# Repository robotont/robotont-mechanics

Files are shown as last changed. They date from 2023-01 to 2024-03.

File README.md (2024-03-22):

# robotont-mechanics

This repository contains models of mechanical parts of Robotont.
The latest release of Robotont is gen3.0.
Gen 3 is developed in SolidWorks (Student version), but a STEP assembly is also provided for modeling, as well as 3MF files for 3D-printing.

## Chassis overview

The main chassis is divided into 5 modules:

+ Frame module
+ Motor module
+ Camera module
+ Computer module
+ Battery module

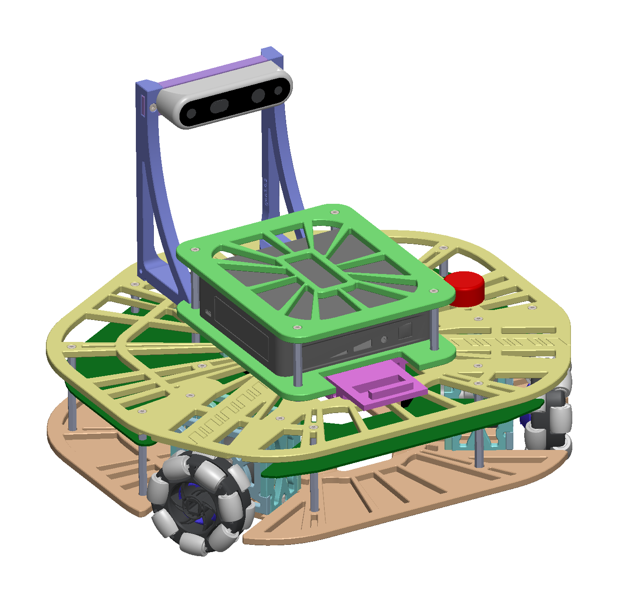
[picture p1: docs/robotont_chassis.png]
Robotont gen3.0 chassis with Intel RealSense and Intel Nuc


## Production

To reproduce Robotont, production files are provided in [production](main-chassis/production/) folder.
The 3MF files contain the print settings optimised for Prusa MK3S, as well as the grouping of parts for printing.

To develop and change Robotont, SolidWorks model files are provided, along with STEP for use with other modeling software.

## Getting started

Print the calibration parts in the [calibration.3mf print project](main-chassis/production/3mf/).
If the two halves fit together and come apart easily, there are no issues with elephant foot and all surfaces are printed cleanly, proceed with printing out all the other print projects in the [3mf folder](main-chassis/production/3mf/).
If there are issues, tune the 3D-printer settings until the calibration piece is printed well, then apply the settings to all of the print projects.

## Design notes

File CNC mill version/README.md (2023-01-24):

# robotont-mechanics
Robotont ver 3.0 is the latest release of the Robotont.

This repository is maintained by Renno Raudmäe renno.raudmae@ut.ee
If you want to make modifications on Robotont and you think that it would be cool if it is available 
for the others as well, then let me know.

Main development is so far done in SolidEdge ST10 - academic version.

Production files are also available in STEP either in STL.

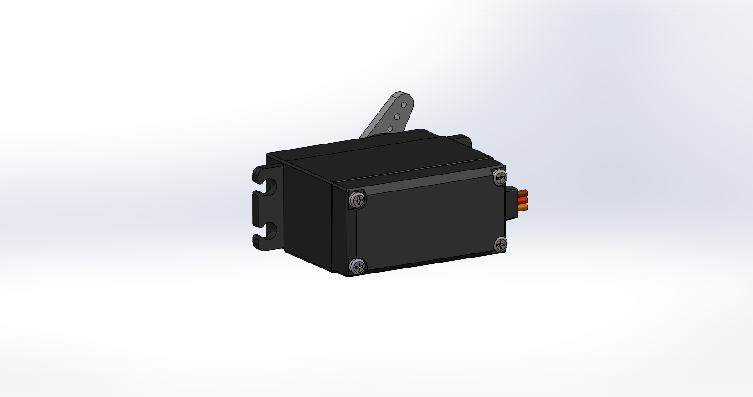
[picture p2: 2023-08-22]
main-chassis/frame_module/extension_servo_slot/towerpro_mg996r_servo/MG996R SBORKA03.PNG

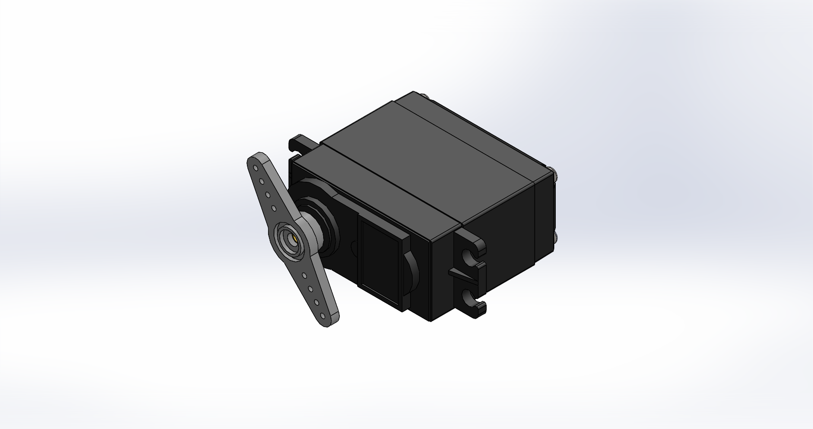
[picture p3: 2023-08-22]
main-chassis/frame_module/extension_servo_slot/towerpro_mg996r_servo/MG996R SBORKA02.PNG

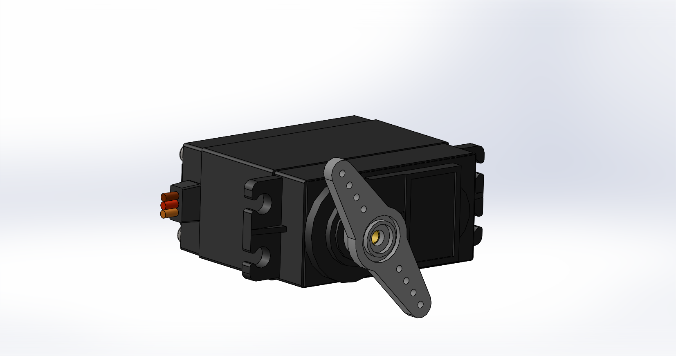
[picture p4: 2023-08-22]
main-chassis/frame_module/extension_servo_slot/towerpro_mg996r_servo/MG996R SBORKA.PNG

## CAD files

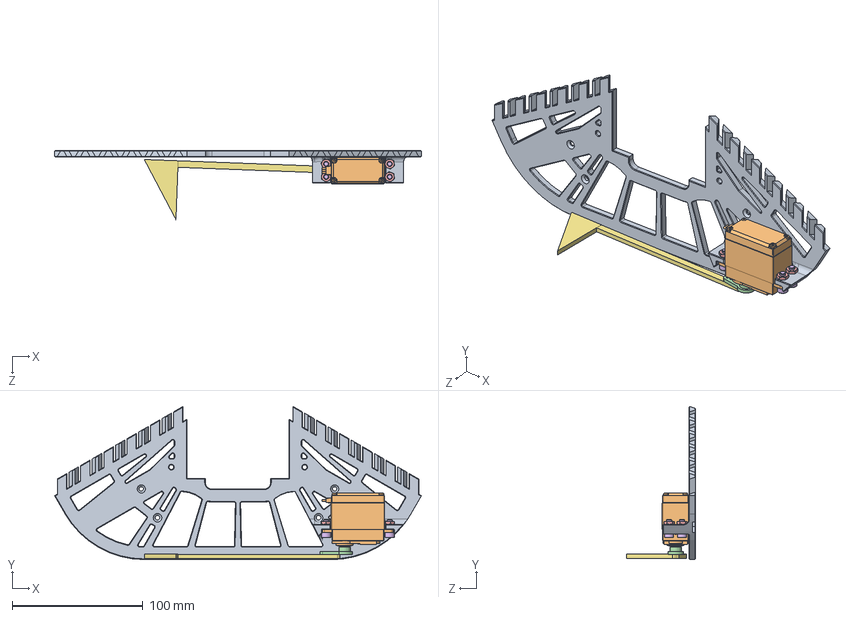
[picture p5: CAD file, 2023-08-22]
main-chassis/frame_module/extension_servo_slot/frame_top_front_servoslot.SLDASM
280.8 x 117.2 x 52.9 mm
top_plate_front_v2-0
Servo MG996R
Servo MG996R Shaft
Servo MG996R arm01
hex thin nut chamfered gradeab_iso x 4
socket head cap screw_iso x 4
demo_flag

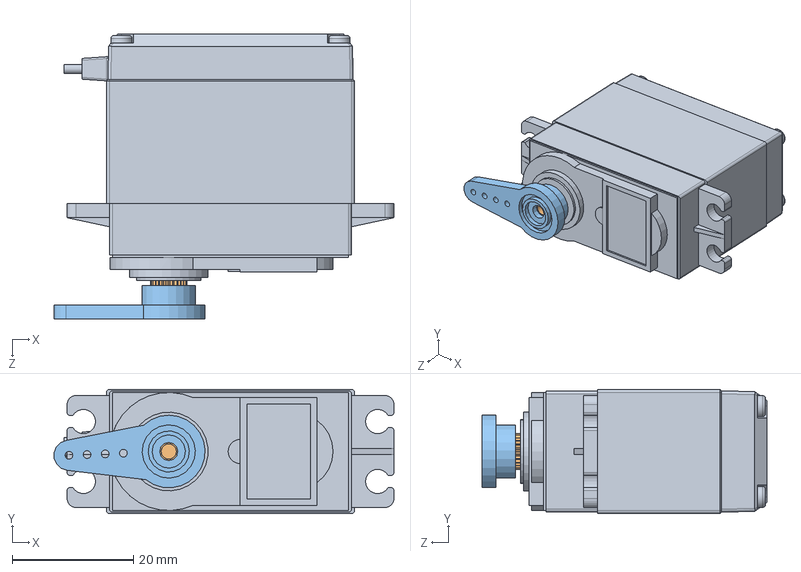
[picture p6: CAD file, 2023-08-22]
main-chassis/frame_module/extension_servo_slot/towerpro_mg996r_servo/MG996R SERVO/MG996R SBORKA.SLDASM
56.2 x 20.5 x 47.0 mm
Servo MG996R
Servo MG996R Shaft
Servo MG996R arm01

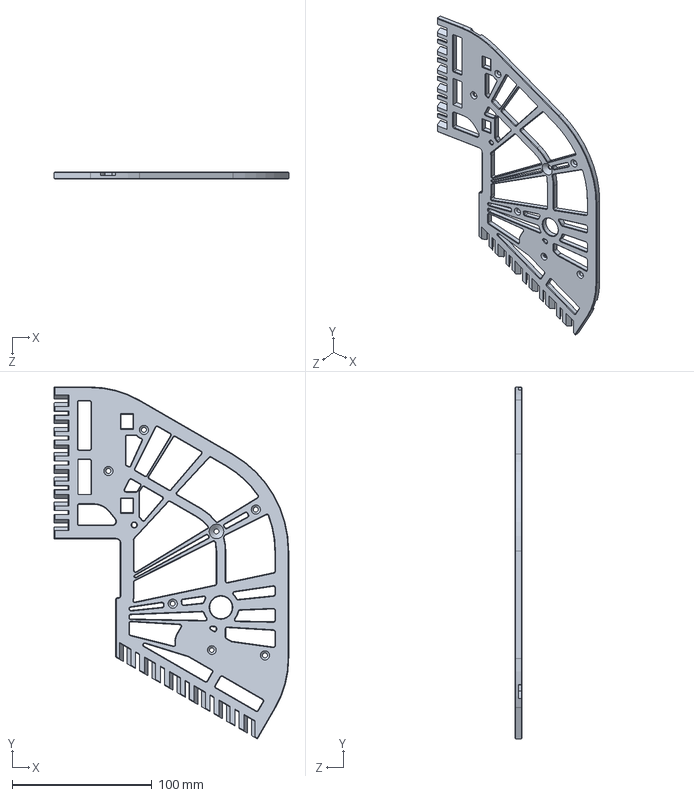
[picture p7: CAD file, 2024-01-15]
main-chassis/frame_module/frame_top.SLDASM
167.8 x 251.8 x 5.00 mm

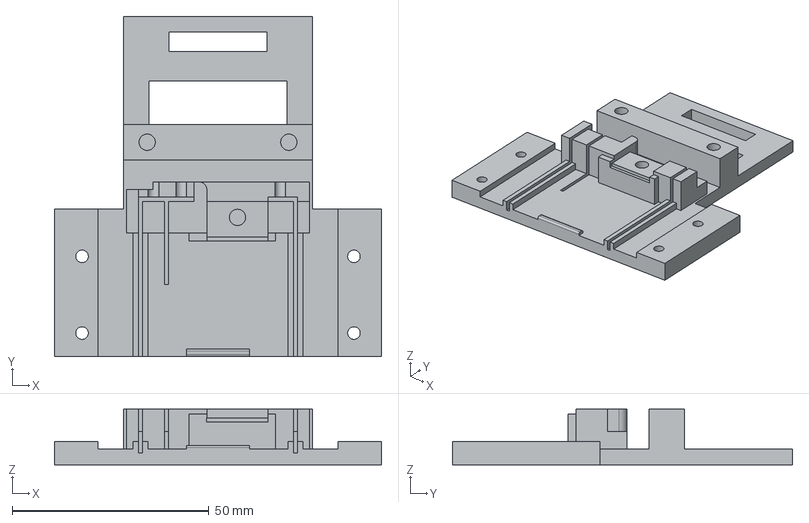
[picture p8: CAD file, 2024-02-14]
main-chassis/battery_module/step/battery_main.stp
83.1 x 86.5 x 14.2 mm

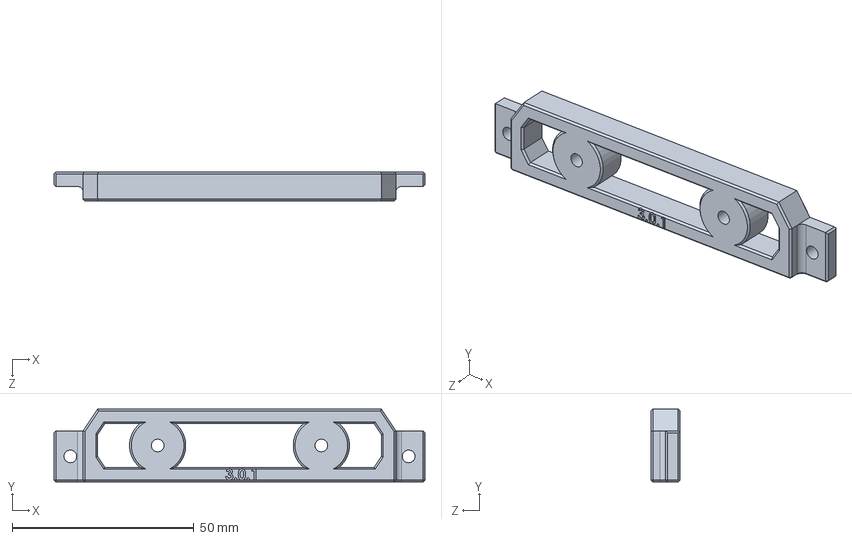
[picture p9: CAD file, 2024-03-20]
main-chassis/camera_module/camera_back.SLDPRT
102.0 x 20.0 x 8.00 mm

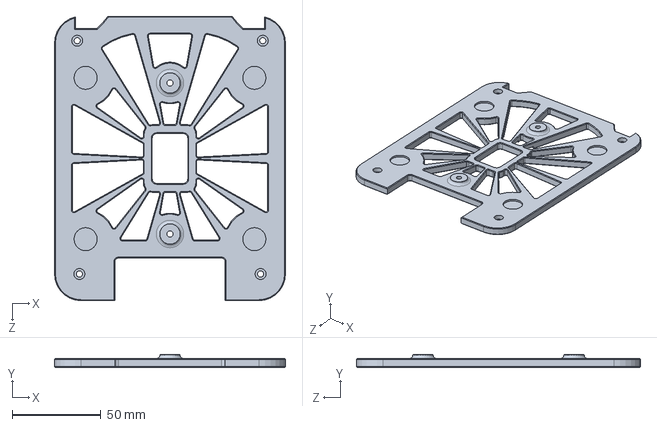
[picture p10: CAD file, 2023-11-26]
main-chassis/computer_module/computer_bottom.SLDPRT
130.0 x 7.20 x 160.0 mm

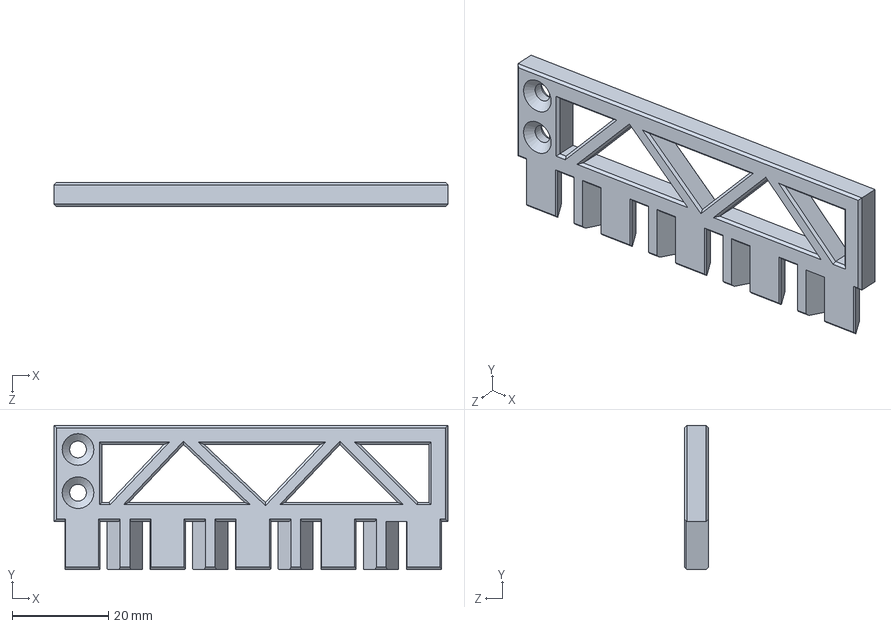
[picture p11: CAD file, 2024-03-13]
main-chassis/extras/calibration_1.SLDPRT
82.0 x 30.0 x 5.00 mm

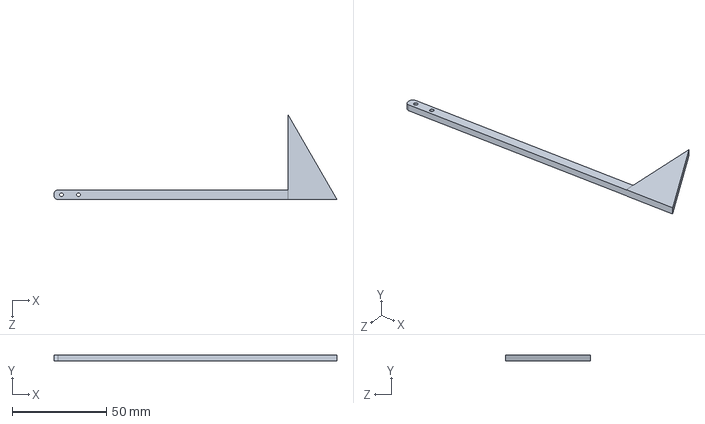
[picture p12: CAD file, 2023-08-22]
main-chassis/frame_module/extension_servo_slot/demo_flag.SLDPRT
150.0 x 3.20 x 45.0 mm

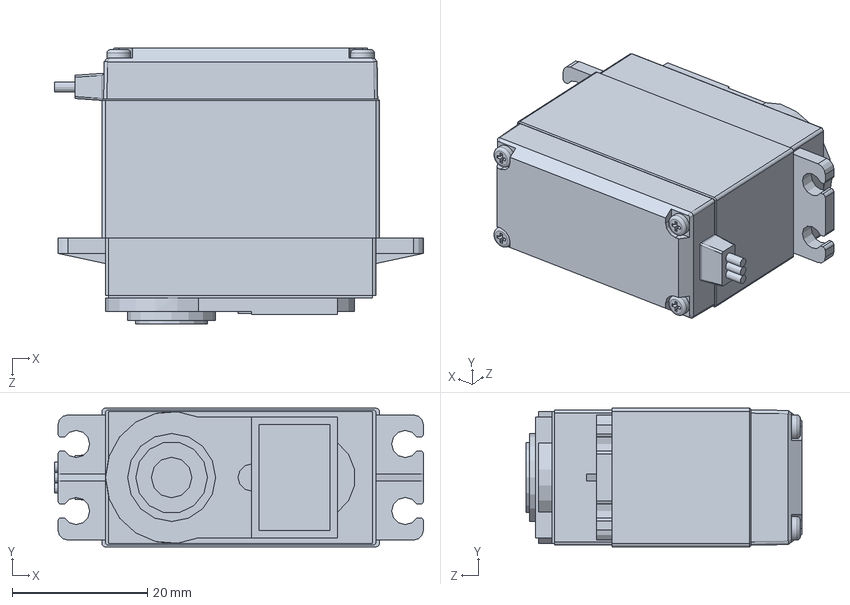
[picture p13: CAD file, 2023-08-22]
main-chassis/frame_module/extension_servo_slot/towerpro_mg996r_servo/MG996R SERVO/Servo MG996R.SLDPRT
54.5 x 20.5 x 40.7 mm

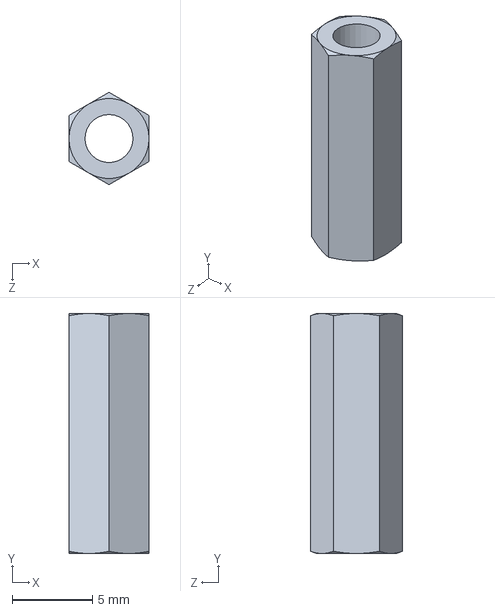
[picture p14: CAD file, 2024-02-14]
main-chassis/frame_module/fastenings/spacer_15mm.SLDPRT
5.00 x 15.0 x 5.77 mm

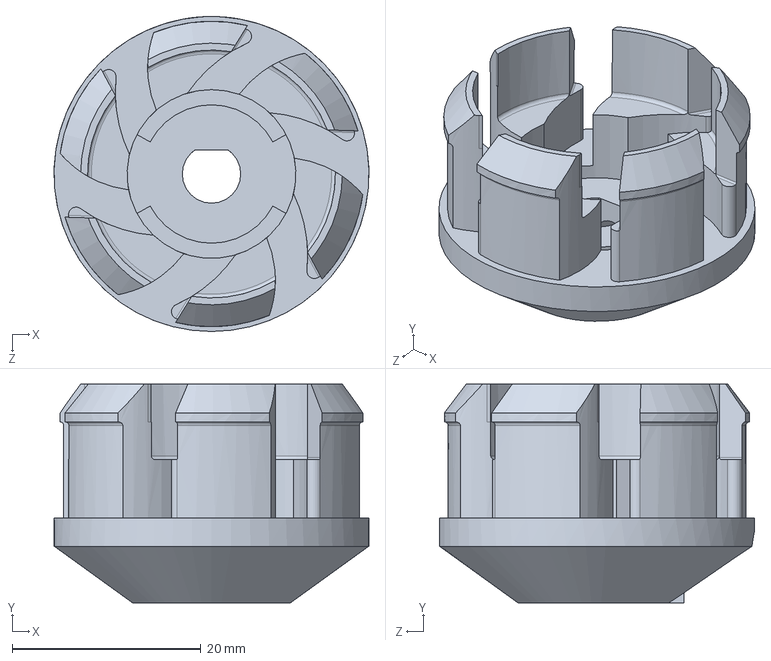
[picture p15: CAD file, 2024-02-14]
main-chassis/motor_module/motor_coupler.SLDPRT
33.4 x 23.2 x 33.4 mm

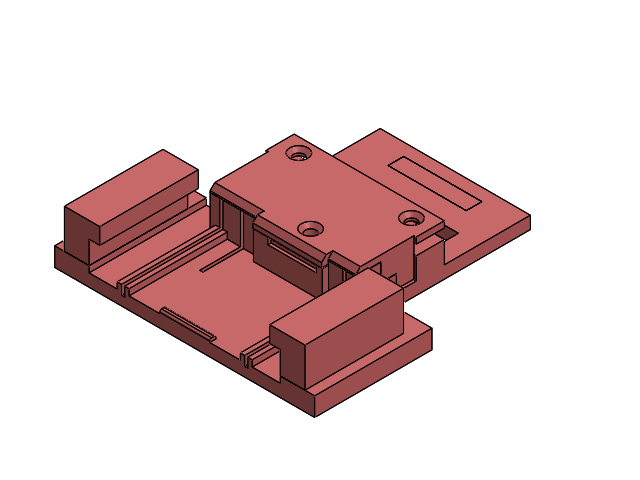
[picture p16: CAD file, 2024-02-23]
main-chassis/battery_module/battery_module.SLDASM
battery_side x 2
battery_main
battery_cap
battery_handle

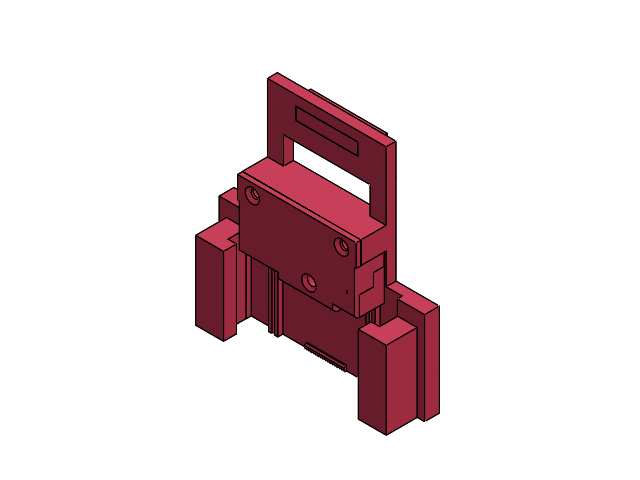
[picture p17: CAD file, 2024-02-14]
main-chassis/battery_module/step/battery_slider.SLDASM
battery_locking_slider
locking_slider_1211_side.stp x 2
handle.stp
Locking_cap.stp

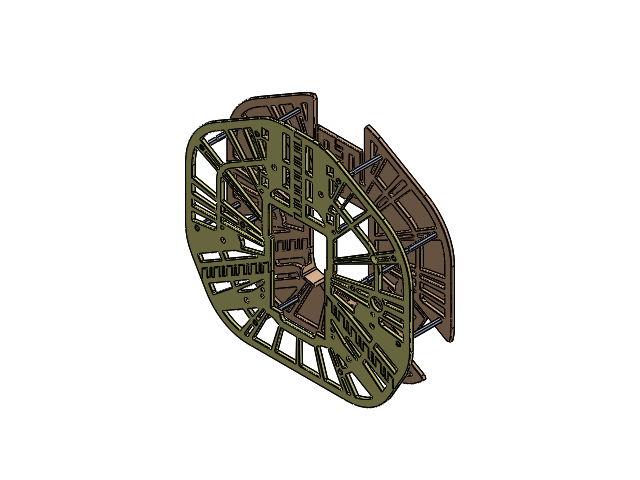
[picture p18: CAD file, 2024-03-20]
main-chassis/frame_module/frame_module.SLDASM
frame_bottom_left
frame_bottom_right
frame_bottom_front
frame_top_left
frame_top_right
frame_top_front
spacer_40mm x 12
spacer_15mm x 12
hexa csunk flathd screw_iso x 22

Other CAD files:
main-chassis/extras/calibration.SLDASM
main-chassis/camera_module/camera_module.SLDASM
main-chassis/frame_module/frame_bottom.SLDASM
main-chassis/production/stl/battery_main.STL
main-chassis/battery_module/battery_cap.SLDPRT
main-chassis/battery_module/battery_handle.SLDPRT
main-chassis/battery_module/battery_main.SLDPRT
main-chassis/battery_module/battery_side.SLDPRT
main-chassis/battery_module/step/battery_cap.stp
main-chassis/battery_module/step/battery_handle.stp
main-chassis/battery_module/step/battery_side.stp
main-chassis/camera_module/Realsense_D435.stp
main-chassis/camera_module/camera_left.SLDPRT
main-chassis/camera_module/camera_right.SLDPRT
main-chassis/computer_module/computer_top.SLDPRT
main-chassis/extras/calibration_2.SLDPRT
main-chassis/extras/encoder_button.SLDPRT
main-chassis/extras/power_button.SLDPRT
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

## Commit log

2022-06-17 Files added into folder
    Files added into folder
    [battery_cap.stp, battery_trigger.stp, bottom_plate.stp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]
2022-12-20 ver 3.0 commit
    ver 3.0 commit
    [276-1902-010 Rev1.cfg, 2_75_Omni-Directional_Wheel.cfg, 3D_print_Tip.stl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]
2023-01-24 assembly fixes January
    assembly fixes January
    [Battery_Trigger_v2.1.1 v2.step, Battery_Trigger_v2.1.1 v2.stp, Battery_cap_v2.1 v1.step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]
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2023-02-16 removed JST connector and shortened pcb length
2023-02-16 modified locking mechanism assembly
    [locking_mechanism.cfg]
2023-02-22 deleted Wheel Module folder
    [276-1902-010 Rev1.cfg, 2_75_Omni-Directional_Wheel.cfg, Linear_tapp_module.cfg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]
2023-02-22 Added Wheel module folder where motor position is adjusted to raise robot clearance from ground
    [276-1902-010 Rev1.cfg, Linear_tapp_module.cfg, omni_wheel_2.75inch.cfg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]
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2023-02-22 changed top plate and bottom plate distance back to original 55mm
    [Robot_assembly_v2.1_grouped.cfg]
2023-02-23 removed double copy part which was duplicated by accident
    [Robot_assembly_v2.1_grouped.cfg]
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2023-06-21 wheel bushing
    3d printabel bushing added
    [moyeux_print.STL, moyeux_print_2.STL, moyeux_print_m3.STL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]
2023-08-22 3D-printable chassis for gen 3.0.
    [BDSG-37-40-R150_motor.stp, MG996R SBORKA.SLDASM, PCB_shape.SLDPRT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]
2023-09-28 Moved camera position 20 mm lower to better fit the robot into the kit.
    [camera_left.SLDPRT, camera_right.SLDPRT]
2023-09-28 Updated frame_bottom_front:
    * Updated model by added supports for keeping the Makita battery from hitting the PCB.
    * Updated assemblies.
    [frame_bottom.SLDASM, frame_bottom_front.SLDPRT, frame_module.SLDASM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]
2023-11-16 Minor: changed colour of camera back plate
    [PCB_shape.SLDPRT, camera_back.SLDPRT, camera_module.SLDASM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]
2023-11-26 Spacer FF -> MF
    [spacer_6mm.SLDPRT]
2023-11-26 Frame module top right gen3.0.2 duplicate file fix
    [frame_top.SLDASM, frame_top_right.SLDPRT, frame_top_right_gen3-0-2.SLDPRT]
2023-11-26 Deleted old redundant version gen3.0.1 of frame module top left.
    [top_plate_back_left.SLDPRT]
2023-11-26 Replaced M3x10 bolts with M3x8 bolts, changed camera module back accordingly.
    [camera_back.SLDPRT, camera_module.SLDASM]
2023-11-26 Added chamfers to camera module back 90-degree inner corners (gen3.0.1).
    [camera_back.SLDPRT, camera_module.SLDASM]
2023-11-26 Replaced Mx10 bolts with M3x8 bolts, mde changes in computer module bottom accordingly. Increased NUC feet holes (d=11.2 -> d=13) to allow NUC gen10 to also fit.
    [computer_bottom.SLDPRT, computer_top.SLDPRT]
2024-01-09 Added new versions to camera module + computer module print projects.
    [cam_comp_1.3mf, cam_comp_2.3mf]
2024-01-09 Added STL files of new versions.
    [camera_back_gen3-0-1.STL, camera_left_gen3-0-2.STL, camera_right_gen3-0-2.STL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]
2024-01-09 Added power button and encoder button models and production files.
    [encoder_and_power_button.3mf, encoder_button.SLDPRT, encoder_button_v4.STL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]
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2024-01-15 Made bolt hole deeper in motor module side.
    [motor_side.SLDPRT]
2024-01-15 Replaced with latest version (gen3.0.3).
    [frame_bottom_front.3mf]
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2024-01-15 Updated motor module pieces production files with latest version of motor module side (gen3-0-3).
    [motor_all.3mf, motor_side_gen3-0-3.STL]
2024-01-15 Added new version of frame bottom front (gen3.0.3) STL file.
    [frame_bottom_front_gen3-0-3.STL]
2024-01-15 Added power button and encoder button.
    [cam_comp_2.3mf]
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2024-01-15 Renamed badly named files.
    [computer_top_gen3-0-0.STL, frame_bottom_left_gen3-0-1.STL, frame_bottom_right_gen3-0-1.STL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]
2024-01-15 Deleted old legacy STL files.
    [bottom_plate_front_gen3-0-1.STL, camera_back_plate_gen3-0-0.STL, camera_side_support_left_gen3-0-1.STL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]
2024-02-14 Minor fixes
    [camera_back.SLDPRT, camera_left.SLDPRT, camera_module.SLDASM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]
2024-02-14 Deleted files with no relevance in gen 3, as they are only related to gen 2.
    [276-1902-010 Rev1.cfg, 3D_print_Tip.stl, 3D_print_Tip.stp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]
2024-02-14 Added motor and omniwheel STEP files.
    [276-1902-003 Rev1.stp.SLDPRT, 276-1902-011 Rev1.stp.SLDPRT, 276-1902-012 Rev1.stp.SLDPRT]
2024-02-14 Added printing files that include the buttons and motor couplers
    [cam_comp_alternative_1.3mf, cam_comp_alternative_2.3mf, motor_all_alternative.3mf]
2024-02-14 Folder refacto: moved folder
    [276-1902-003 Rev1.stp.SLDPRT, 276-1902-011 Rev1.stp.SLDPRT, 276-1902-012 Rev1.stp.SLDPRT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]
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2024-02-14 Nothing changed, just rebuild of assembly.
    [camera_module.SLDASM, frame_module.SLDASM]
2024-02-14 Folder refacto: moved files
    [encoder_button.SLDPRT, encoder_button_v4.STL, power_button.SLDPRT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]
2024-02-14 Folder refacto: added folder for models used for visualisation, but not printed
    [PCB_shape.SLDPRT, e-stop_button.SLDPRT, e-stop_nut.SLDPRT]
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2024-02-14 Folder refacto: moved motor coupler to correct place
    [motor_coupler.SLDPRT]
2024-02-14 Folder refacto: added separate folder for battery locking slider module.
    [battery_cap.stp, battery_handle.stp, battery_locking_slider.SLDPRT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]
2024-02-14 Added missing STL files
    [battery_cap.STL, battery_handle.STL, battery_main.STL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]
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2024-02-14 Rebuilt battery module in SolidWorks. Kept the old files for now in separate folder.
    [battery_cap.SLDPRT, battery_cap.stp, battery_handle.SLDPRT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]
2024-03-12 Renamed extra objects to include the word extra in name.
    [extra_encoder_button_v4.STL, extra_power_button_v3.STL]
2024-03-12 Added calibration parts for calibrating printer for successful Robotont print.
    [calibration.3mf, calibration.SLDASM, calibration_1.SLDPRT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]
2024-03-13 Removed legacy print projects and cleaned up naming.
    [cam_comp_1.3mf, cam_comp_2.3mf, cam_comp_alternative_1.3mf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]
2024-03-13 Cleaned up model naming inside print files.
    [frame_bottom_left.3mf, frame_bottom_right.3mf, frame_top_front.3mf]
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2024-03-13 Minor: changed model colour, added explode sketch lines.
    [calibration.SLDASM, calibration_1.SLDPRT]
2024-03-20 Evened out bed temperature between different print projects.
    [calibration.3mf, frame_bottom_front.3mf, frame_bottom_left.3mf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]
2024-03-20 Made version number visible again.
    [camera_back.SLDPRT, camera_left.SLDPRT, camera_module.SLDASM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]
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
